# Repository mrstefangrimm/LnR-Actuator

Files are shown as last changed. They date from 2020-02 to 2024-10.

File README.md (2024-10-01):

# LnR-Actuator
The linear and rotary (LnR) actuator is a electromechanical device that allows linear as well as rotary motion of the shaft.

## Project History
A first revision was released in 2018. The construction has been simplified and made stiffer since then. All *[released revisions](https://github.com/mrstefangrimm/LnR-Actuator/releases)* are mechanical compatible. 

## Construction
A detailed description how to build a LnR-Actuator is published on *[Instructables.com](https://www.instructables.com/id/Linear-and-Rotation-Actuator/)* and [instructions for rev. 4 with brass bearings](https://www.instructables.com/Linear-and-Rotary-Actuator-With-Brass-Bearings/). 

## Manufacturing Tool Chain

| Software | License |
| --- | --- |
| SketchUp | SketchUp Shop |
| Ultimaker Cura | GPL |

## Software Tool Chain

| Application | License |
| --- | --- |
| lnr | Apache license |

| Tool | License |
| --- | --- |
| Visual Studio Code  | Microsoft license  |

| Library | Licence |
| --- | --- |
| angular | MIT license |
| Node.js | MIT license |

## Reference Projects

 - *[Marker Motion X-Ray Imaging Phantom](https://github.com/mrstefangrimm/GRIS5A)*
 - *[Liver Deformation X-Ray Imaging Phantom](https://github.com/mrstefangrimm/No2)*
 - *[Lung Motion X-Ray Imaging Phantom](https://github.com/mrstefangrimm/No3)*

## License


This work is licensed under the Creative Commons Attribution-ShareAlike 4.0 International License. To view a copy of this license, visit http://creativecommons.org/licenses/by-sa/4.0/ or send a letter to Creative Commons, PO Box 1866, Mountain View, CA 94042, USA.

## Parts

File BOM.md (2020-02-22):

Anz. | Beschreibung
---- | ------------ 
1 | Standard Servo Motor Tower Pro MG946R mit mitgeliefertem Servo Arm, 4 Befestigungsschrauben und vier Messinghülsen
1 | Micro Servo Motor Tower Pro MG90S mit mitgeliefertem Servo Arm und 2 Befestigungsschrauben
2 | Stahl Rundprofil d4 x 166 mit M4 x 15 Gewinde an einer Seite
1 | Stahl Rundprofil d4 x 14 mit Seegerringkerben mit Abstand 8 mm
1 | Stahl Rundprofil d4 x 12
1 | Holz Rundprofil d6 x 120
11 | M2 x 10 Universal Senkkopfschraube mit S-Spitze
4 | M4 Unterlagsscheibe
6 | M4 Mutter
2 | Seegerring d4
1 | Bueroklammer d1
1 | LnR-ChassisLinks oder LnR-ChassisRechts
1 | LnR-ChassisHaube
1 | LnR-ReiterLinks oder LnR-ReiterRechts
1 | LnR-ReiterLinksDeckel oder LnR-ReiterRechtsDeckel
1 | LnR-Flansch-Kreuz
1 | LnR-Verlaengerung
2 | LnR-SchraubVerstaerkung



This work is licensed under the Creative Commons Attribution-ShareAlike 4.0 International License. To view a copy of this license, visit http://creativecommons.org/licenses/by-sa/4.0/ or send a letter to Creative Commons, PO Box 1866, Mountain View, CA 94042, USA.

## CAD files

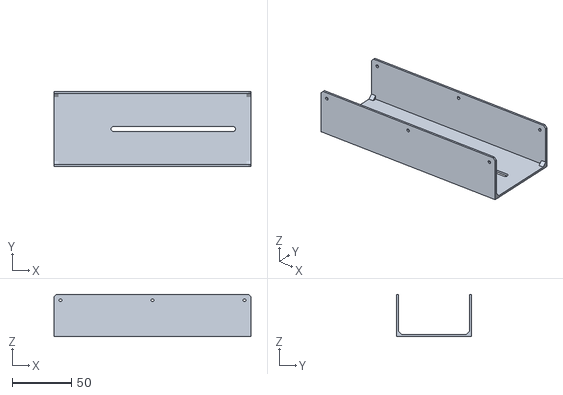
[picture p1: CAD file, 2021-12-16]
Instructable/Rev4/STLFiles/LnR-Cover.stl
166.0 x 63.2 x 35.6

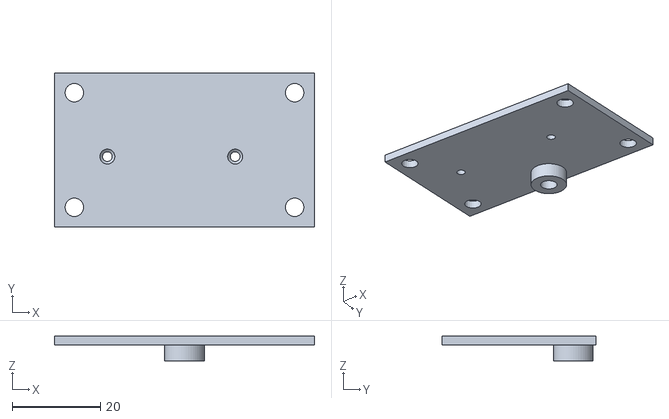
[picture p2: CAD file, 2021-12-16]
Instructable/Rev4/STLFiles/LnR-CarriageLeftLid.stl
59.0 x 35.0 x 5.60

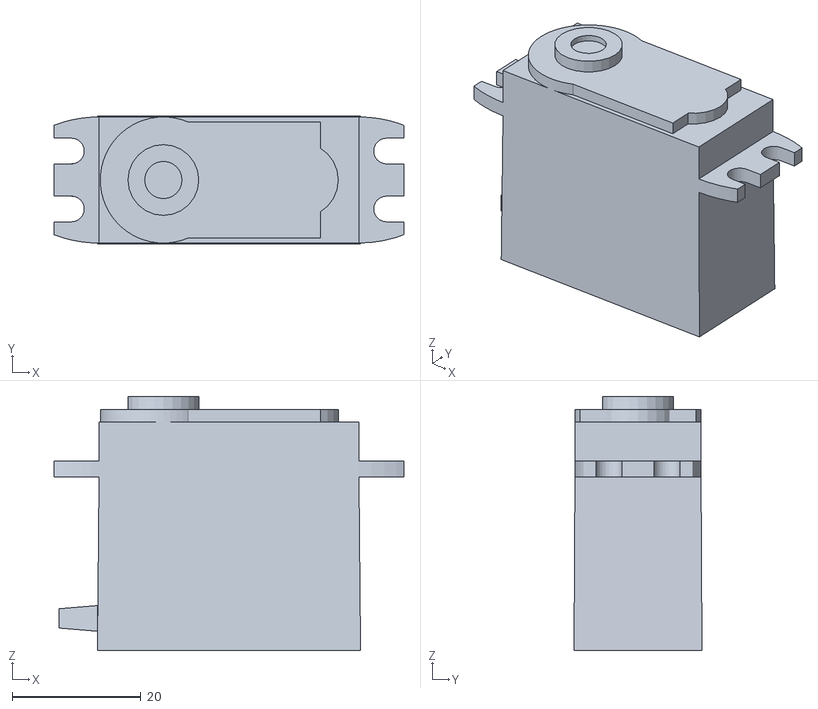
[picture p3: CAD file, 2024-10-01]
Soffware/lnr/public/LnR-VirmsGroupStaticBaseAnthracite.obj
54.4 x 19.9 x 39.5

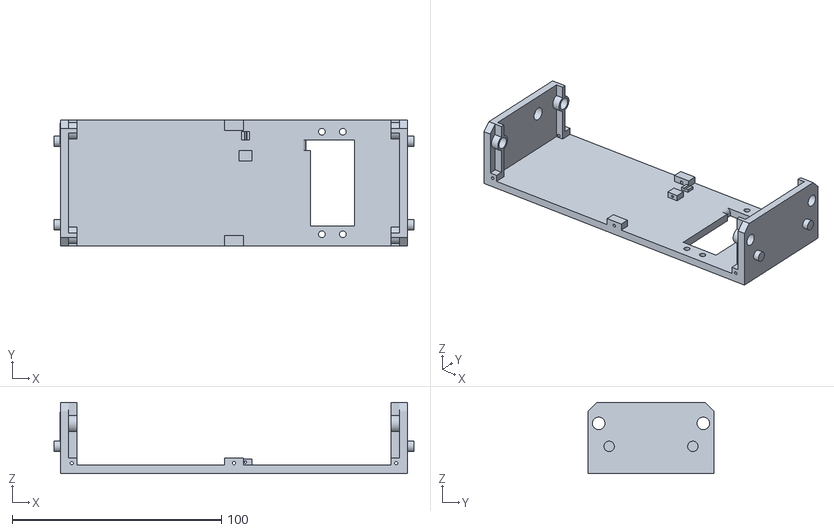
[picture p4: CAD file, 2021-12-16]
Instructable/Rev4/STLFiles/LnR-BaseLeft-Rev4.stl
172.0 x 60.0 x 34.0

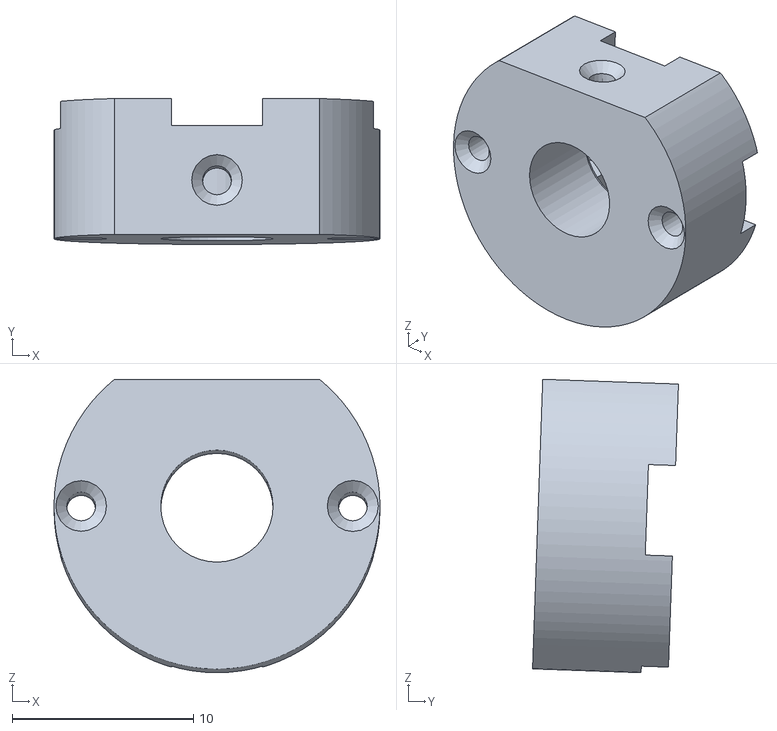
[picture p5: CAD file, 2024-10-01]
Soffware/lnr/public/LnR-VirmsGroupRotationBlue.obj
18.0 x 8.06 x 16.2

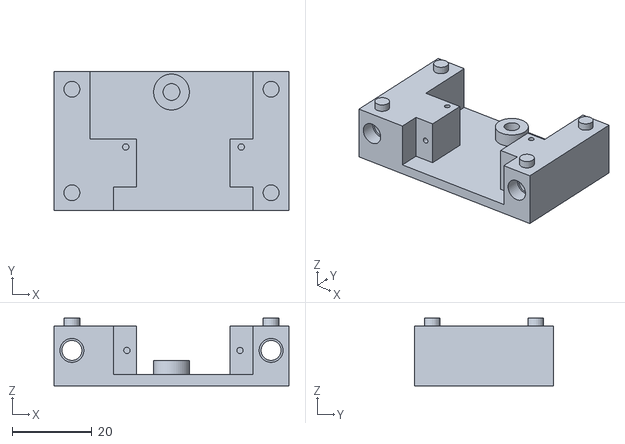
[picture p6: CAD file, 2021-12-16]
Instructable/Rev4/STLFiles/LnR-CarriageRight-JX9180MG.stl
59.0 x 35.0 x 17.0

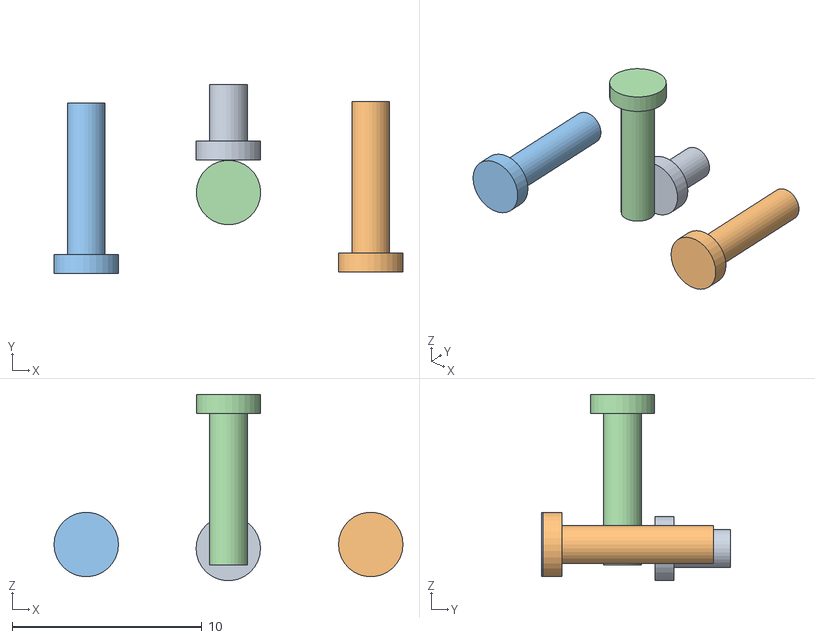
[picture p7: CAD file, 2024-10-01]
Soffware/lnr/public/LnR-VirmsGroupRotationSilver.obj
18.4 x 9.98 x 9.81
Lib_M2x3_1_1
Lib_M2x8_1_1
Lib_M2x8_1_2
Lib_M2x8_1_3

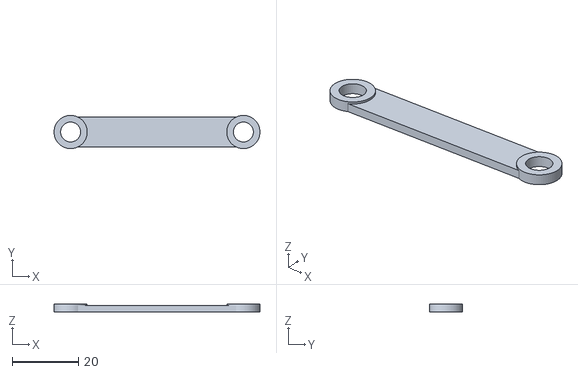
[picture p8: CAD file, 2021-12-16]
Instructable/Rev4/STLFiles/LnR-ExtensionArm-Rev4.stl
62.0 x 10.0 x 2.50

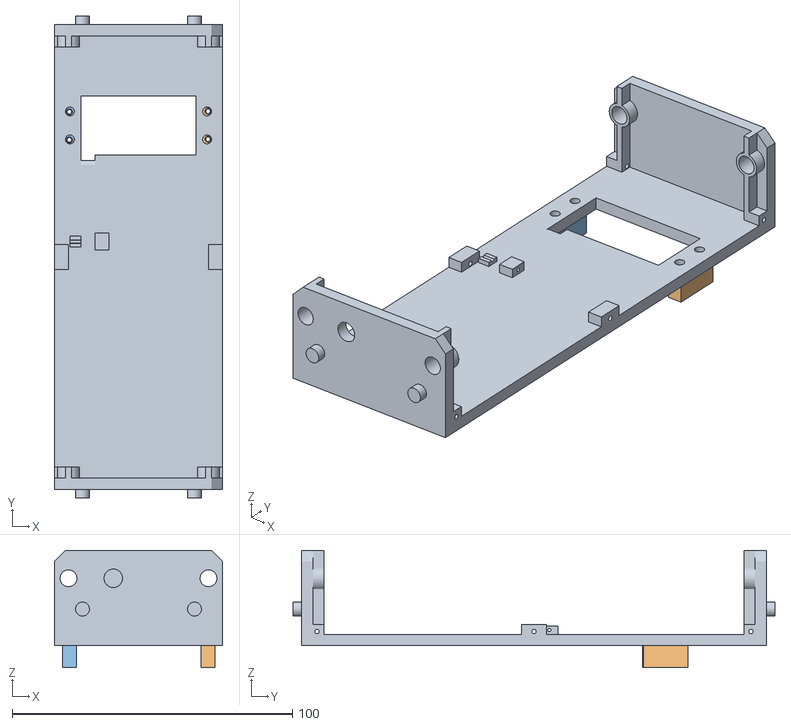
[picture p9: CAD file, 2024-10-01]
Soffware/lnr/public/LnR-VirmsGroupStaticBaseBlue.obj
60.0 x 172.0 x 42.0
LnR_ChassisLinks_Rev4_1
LnR_SchraubVerstaerkung1
LnR_SchraubVerstaerkung2

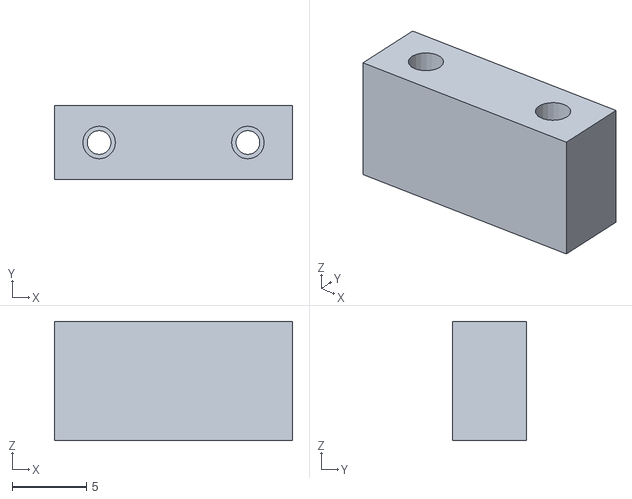
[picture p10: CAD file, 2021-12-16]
Instructable/Rev4/STLFiles/LnR-ServoFixationBlock.stl
16.0 x 5.00 x 8.00

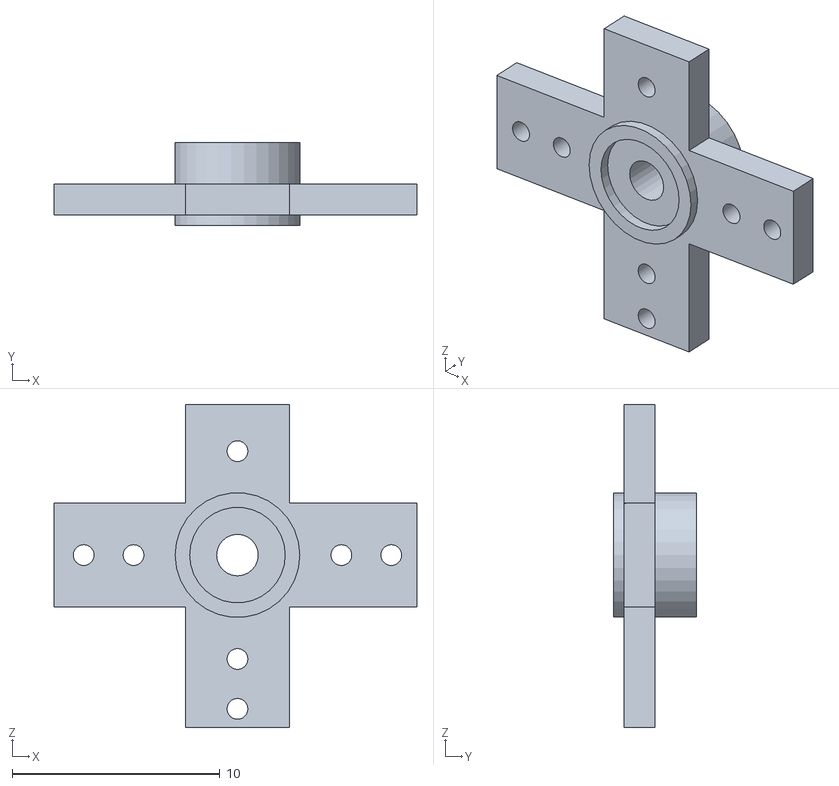
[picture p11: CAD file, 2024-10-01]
Soffware/lnr/public/LnR-VirmsGroupRotationWhite.obj
17.5 x 4.00 x 15.6

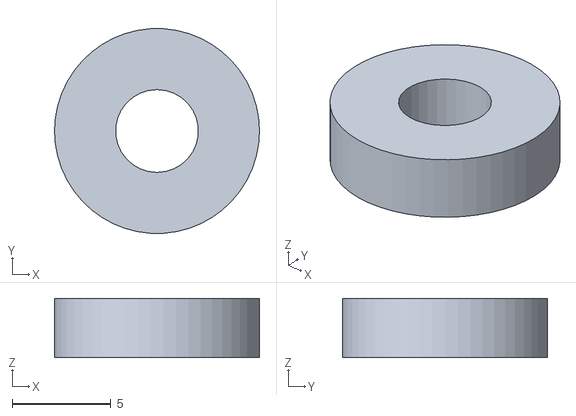
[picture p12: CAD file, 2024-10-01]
Soffware/lnr/public/LnR-VirmsGroupServoArmBlue.obj
10.4 x 10.4 x 3.00

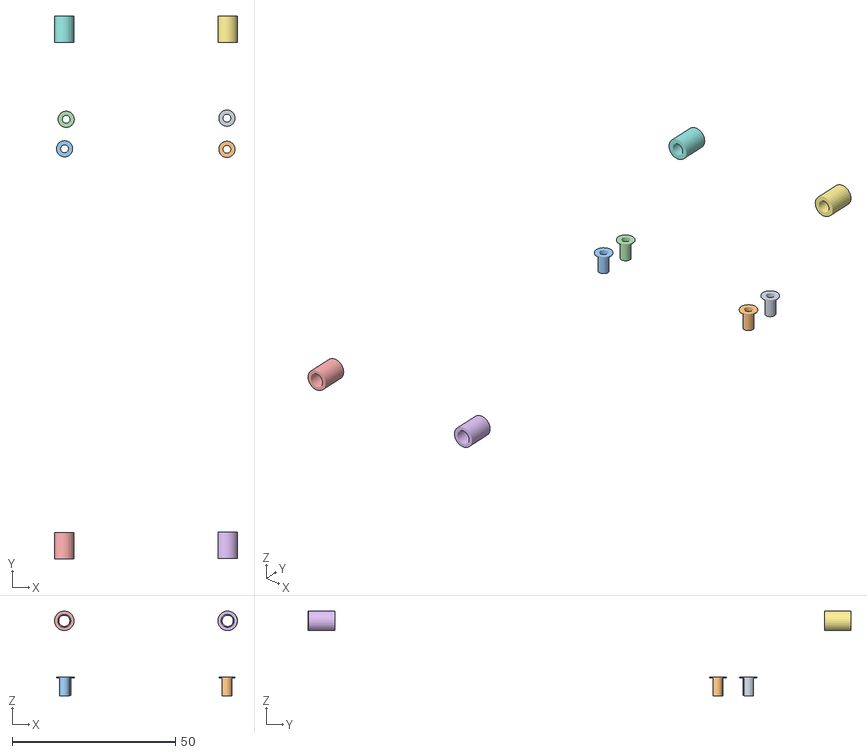
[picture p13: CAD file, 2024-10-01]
Soffware/lnr/public/LnR-VirmsGroupStaticBaseGold.obj
56.0 x 166.1 x 26.0
Lib_MG996R_BrassSleeve1
Lib_MG996R_BrassSleeve2
Lib_MG996R_BrassSleeve3
Lib_MG996R_BrassSleeve4
LnR_BrassSleeve_6x4x8_1
LnR_BrassSleeve_6x4x8_2
LnR_BrassThreadedSleeve_6x3_3x8_1
LnR_BrassThreadedSleeve_6x3_3x8_2

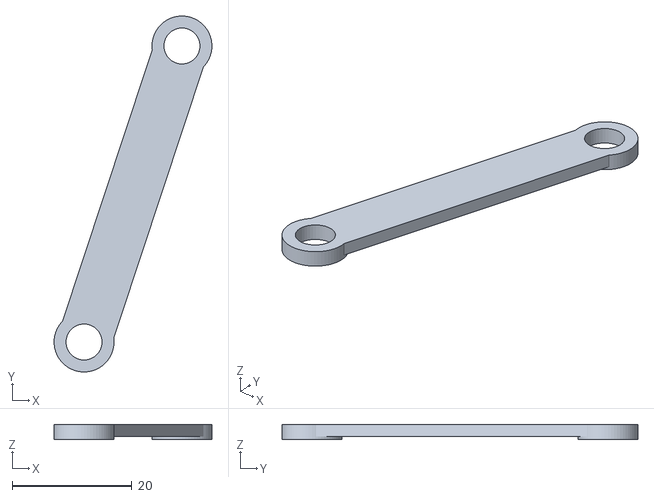
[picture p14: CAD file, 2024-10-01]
Soffware/lnr/public/LnR-VirmsGroupExtensionArm.obj
26.3 x 59.4 x 2.50

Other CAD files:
Soffware/lnr/public/LnR-VirmsGroupStaticCoverBlue.obj
Instructable/Rev4/STLFiles/LnR-CarriageLeft-JX9180MG.stl
Instructable/Rev4/STLFiles/LnR-BaseRight-Rev4.stl
Instructable/Rev4/STLFiles/LnR-ServoArmFixationRing.stl
Accessories/Sketchup/Cmn-FlanschHalter.skp
Accessories/Sketchup/Gris5a-Flansch.skp
Accessories/Sketchup/LnR-Calibration-Basis.skp
Accessories/Sketchup/LnR-Calibration-Messaufsatz.skp
Instructable/Rev3/STLFiles/LnR-BaseLeft.stl
Instructable/Rev3/STLFiles/LnR-BaseRight.stl
Instructable/Rev3/STLFiles/LnR-CarriageLeft.stl
Instructable/Rev3/STLFiles/LnR-CarriageLeftLid.stl
Instructable/Rev3/STLFiles/LnR-CarriageRight.stl
Instructable/Rev3/STLFiles/LnR-CarriageRightLid.stl
Instructable/Rev3/STLFiles/LnR-Cover.stl
Instructable/Rev3/STLFiles/LnR-ExtensionArm.stl
Instructable/Rev3/STLFiles/LnR-Flange.stl
Instructable/Rev3/STLFiles/LnR-ServoArmFixationRing.stl
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

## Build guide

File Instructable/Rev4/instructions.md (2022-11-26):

# Linear and Rotary Actuator With Brass Bearings

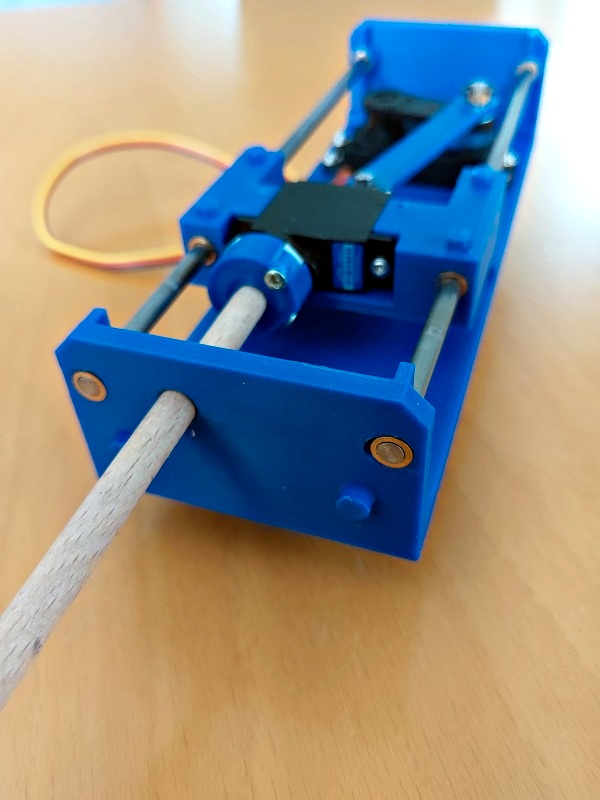
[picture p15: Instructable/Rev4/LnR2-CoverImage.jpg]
LnR2-CoverImage


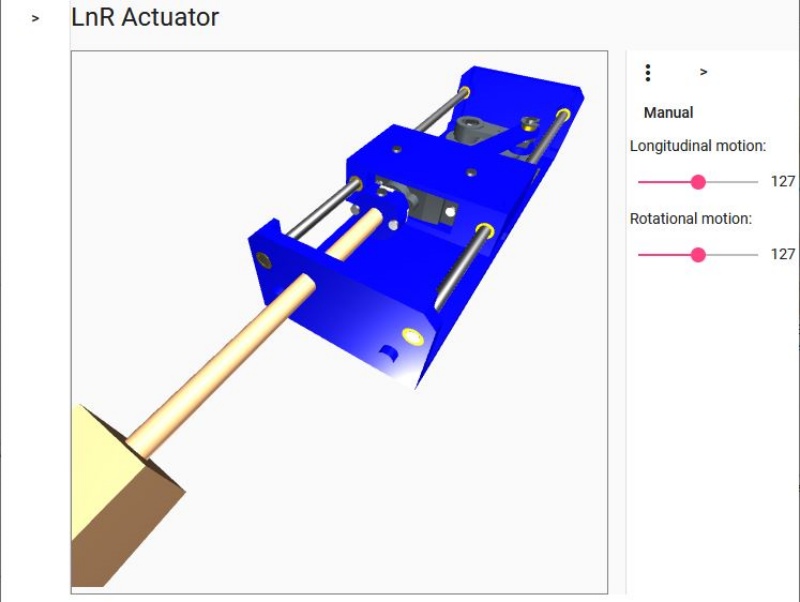
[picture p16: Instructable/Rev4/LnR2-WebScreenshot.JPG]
LnR2-WebScreenshot


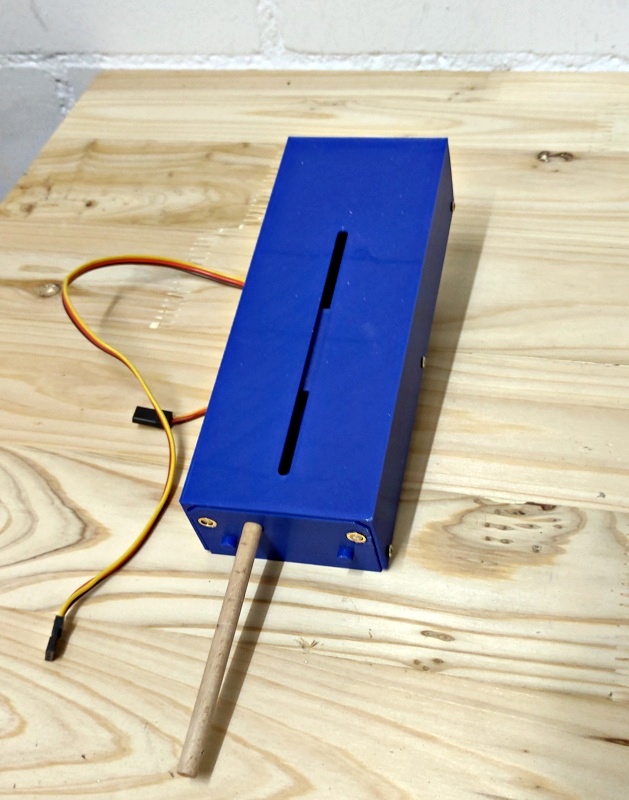
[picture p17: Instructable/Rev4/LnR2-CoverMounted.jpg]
LnR2-CoverMounted


The Linear and Rotary (LnR) actuator is a linear servo with a rotatable shaft. This means you can move an  object forwards and backwards and rotate it at the same time. It is  possible to move an object 45 mm back and forth and rotate it 180 degrees.

To get an idea, check out the [3D model of the LnR Actuator](https://mrstefangrimm.github.io/). With the two sliders on the right you can simulate longitudinal and rotational motion.

The used motors are two commercially available servo motors. Beside the low price, servos have a useful characteristic: Servos have already integrated control logic in order to be absolutely positioned. Additional position read-out modules are therefore not required.

To  build it you need a lathe and metal drills (4.1 and 3.3 mm) to manufacture the sleeve bearings. A turning tool to create the snap ring notch is also required. Further you need a M4 screw tap and a M4 thread cutter.

This is a improved version of the [Linear and Rotary Actuator](https://www.instructables.com/Linear-and-Rotation-Actuator/). The advantages are:

- It makes less noise
- It is more accurate because it has less mechanical play and less friction

To build this improved version of the LnR Actuator, you will need a lathe to manufacture the sleeve bearings. The original LnR Actuator was explicitly designed so that it can be manufactured with of-the-shelve components.

The direct material costs are approximately USD 30.

**Supplies**

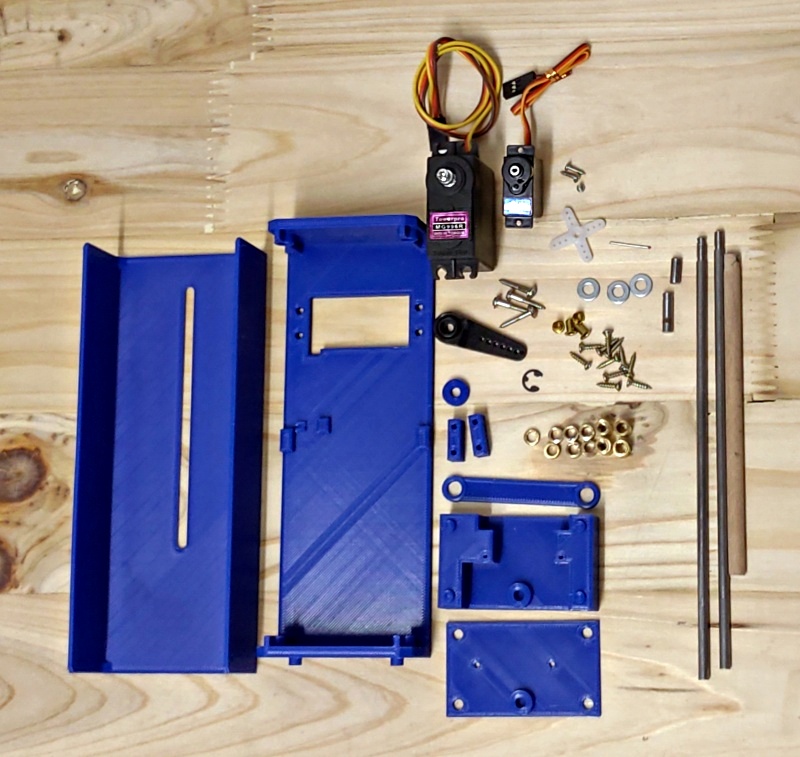
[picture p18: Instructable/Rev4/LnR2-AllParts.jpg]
LnR2-AllParts


 1 Standard Servo Tower Pro MG946R. Comes with servo arm, 4 M2 mounting screws and 4 d3 brass sleeves

 1 Micro Servo JX PDI 9180MG. Comes  with servo arm and 2 mounting screws 

11 M2 x l10 mm flat headed screw

 2 Brass sleeve d6 x l8

 2 Threaded brass sleeve d6 x l8

 4 Brass sleeve d6 x l4

 2 Brass sleeve d6 x l3

 1 Brass sleeve d6 x l2

 3 M4 washer

 1 Snap ring d4

 1 Paperclip d1

 1 Wooden rod 6 x l120 

 2 Steel shaft d4 x l166 with M4 x l8 thread on one end 

 1 Steel rod d4 x l15 with a snap ring notch 

 1 Steel rod d4 x l12

 1 3D Printer

 105g PLA filament

 1 Lathe machine

 Legend: l:length in millimeters, d:diameter in millimeters

## Step 1: 3D Printed Parts

You either need to print the left-sided or  right-sided parts. The pictures in this Instructable show a left-sided  LnR Actuator.

You can use PLA with 20% infill. If you do not have a 3D printer, I recommend looking for a 3D printing service nearby.

## Step 2: Rotary Drive

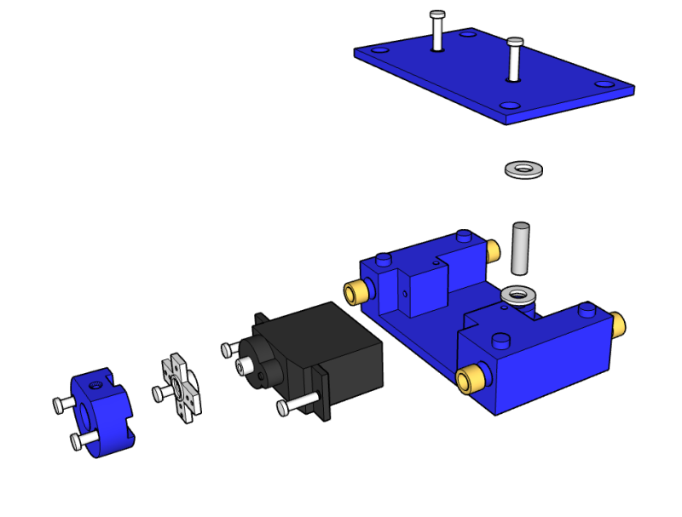
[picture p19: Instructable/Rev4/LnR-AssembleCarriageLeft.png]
LnR-AssembleCarriageLeft


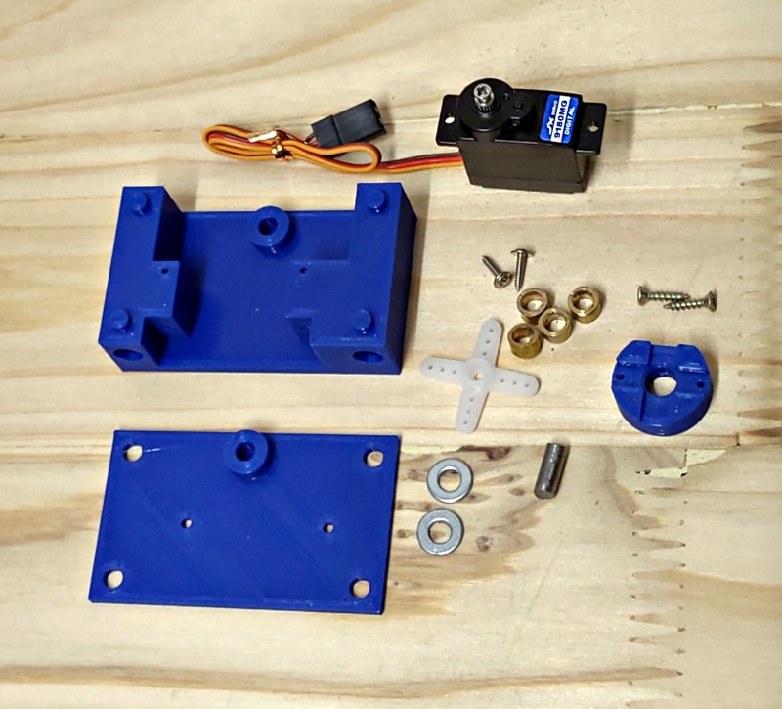
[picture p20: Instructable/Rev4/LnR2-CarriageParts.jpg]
LnR2-CarriageParts


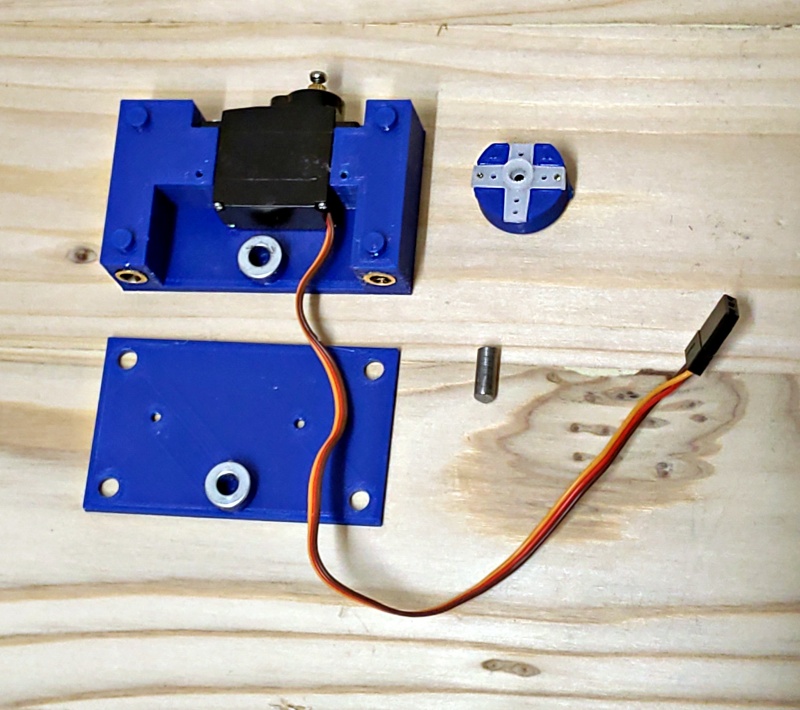
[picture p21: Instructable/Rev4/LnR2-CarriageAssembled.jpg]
LnR2-CarriageAssembled


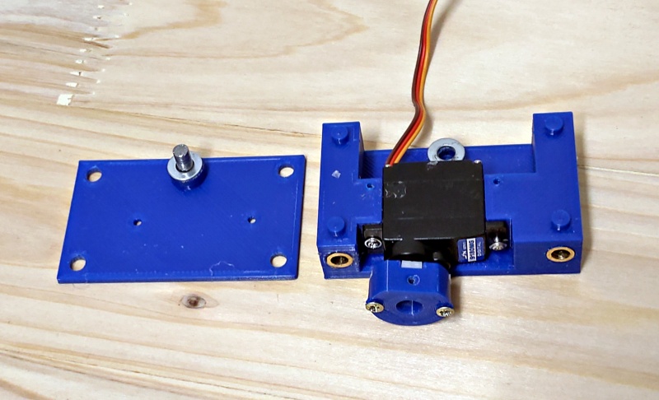
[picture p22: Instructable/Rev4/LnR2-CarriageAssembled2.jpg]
LnR2-CarriageAssembled2


Press the 4 mm long brass sleeves into the printed carriage component. This is best done in a vice. Mount the micro servo with the supplied screws.

Use 2 M2 screws to attach the supplied servo cross arm to the printed flange.

Glue 2 M4 washers onto the carriage and the carriage lid.

## Step 3: Linear Drive

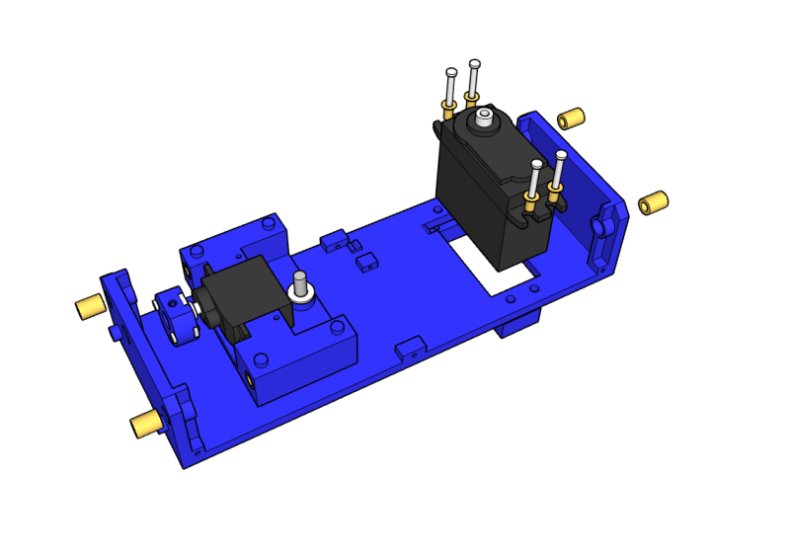
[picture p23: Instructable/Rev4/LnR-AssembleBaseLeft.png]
LnR-AssembleBaseLeft


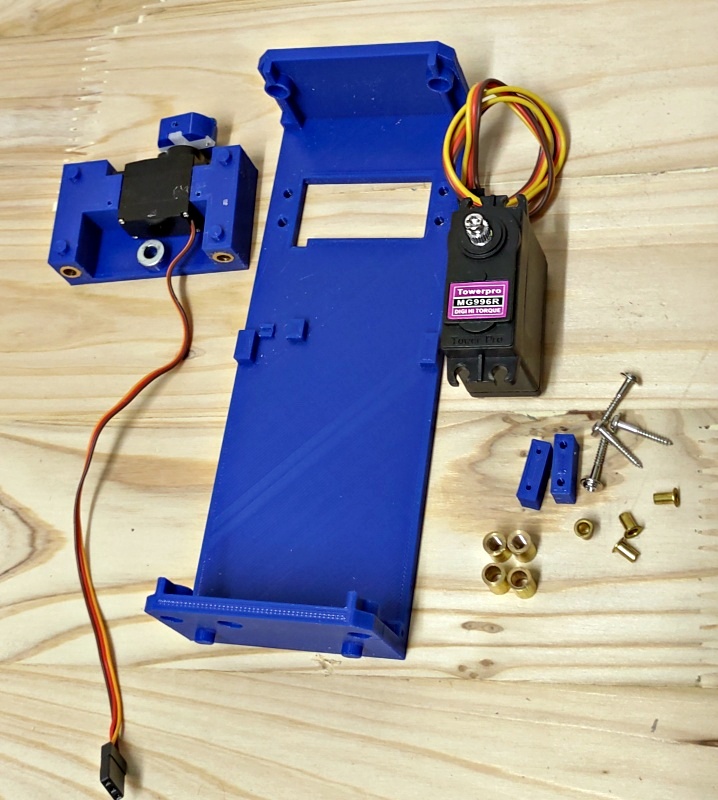
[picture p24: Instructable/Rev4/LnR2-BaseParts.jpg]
LnR2-BaseParts


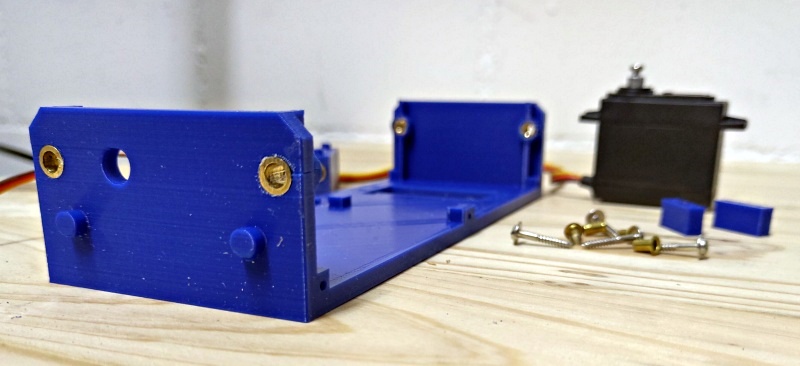
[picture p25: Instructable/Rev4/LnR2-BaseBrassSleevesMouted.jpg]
LnR2-BaseBrassSleevesMouted


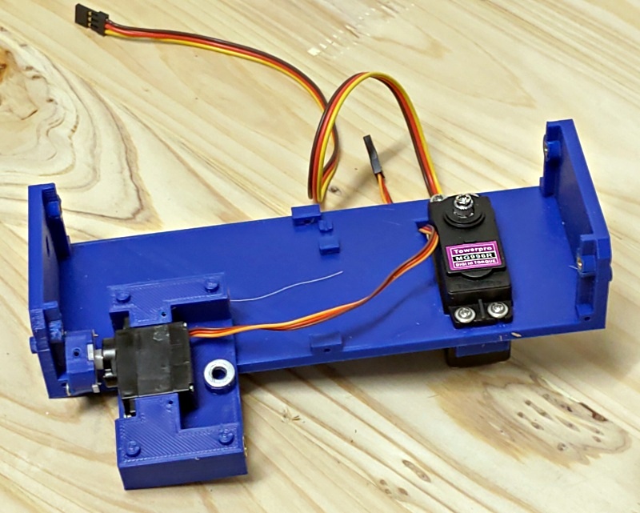
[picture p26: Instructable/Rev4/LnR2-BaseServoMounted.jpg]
LnR2-BaseServoMounted


Press the 8 mm long brass sleeves into the printed base component. This is best done in a vice. The plain sleeves are mounted to the front and the threaded sleeves are mounted to the rear plane.

Attach the standard servo motor the the printed base component. In order to bring the servo through the opening, you need to  remove its bottom cap and bend the cable down. As shown in the picture, the cable of the micro servo has to go through the intended opening first. For fastening the servo motor, use supplied screws and brass hulls and the two printed servo fixation blocks.

## Step 4: Longitudinal Guides

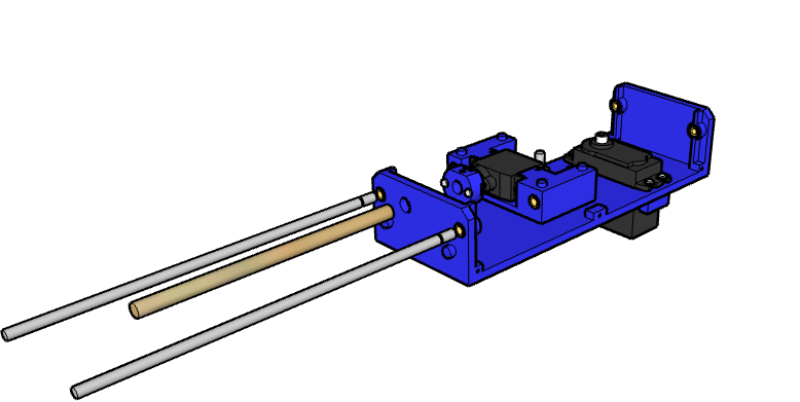
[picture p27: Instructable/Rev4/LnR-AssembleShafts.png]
LnR-AssembleShafts


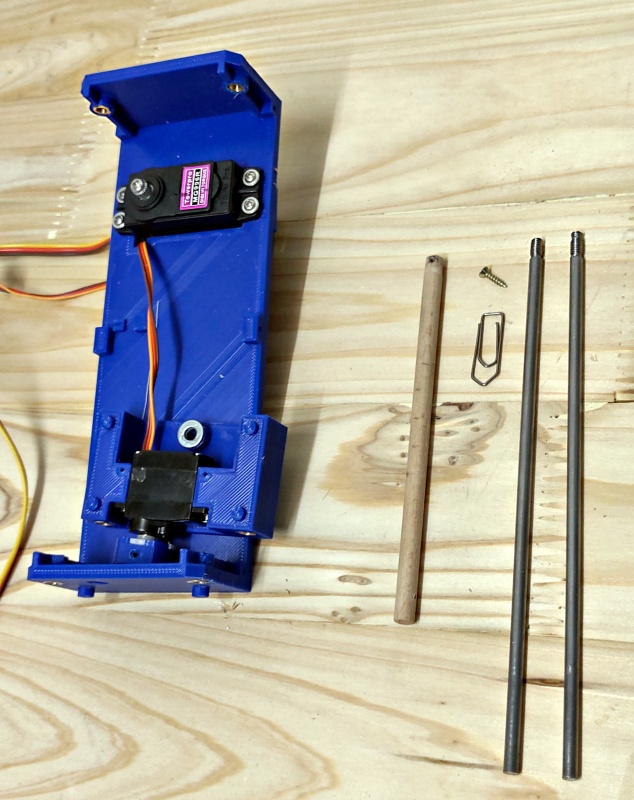
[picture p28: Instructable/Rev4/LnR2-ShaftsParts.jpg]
LnR2-ShaftsParts


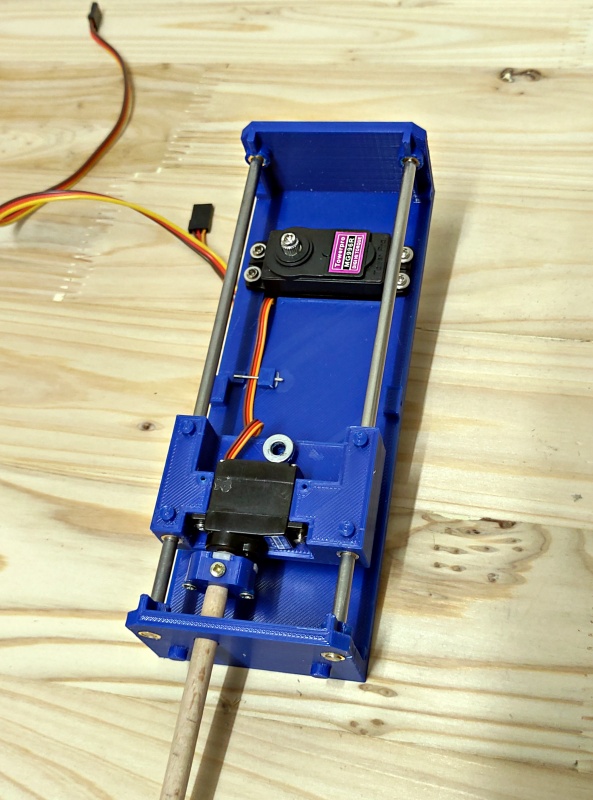
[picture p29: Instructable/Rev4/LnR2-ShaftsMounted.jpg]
LnR2-ShaftsMounted


Slide the metal shafts from the front through the sleeve bearings of the base component and the carriage component. Then screw the shafts into the threaded sleeves on rear plane of the base component.

Attach the wooden rod the flange with a M2 screw. Drill a 1.5 mm hole into the wooden rod where the screw goes through, otherwise the wood will break.

Use one leg of the paperclip to fixate the cable of the micro servo the the base component.

## Step 5: Force Transmission

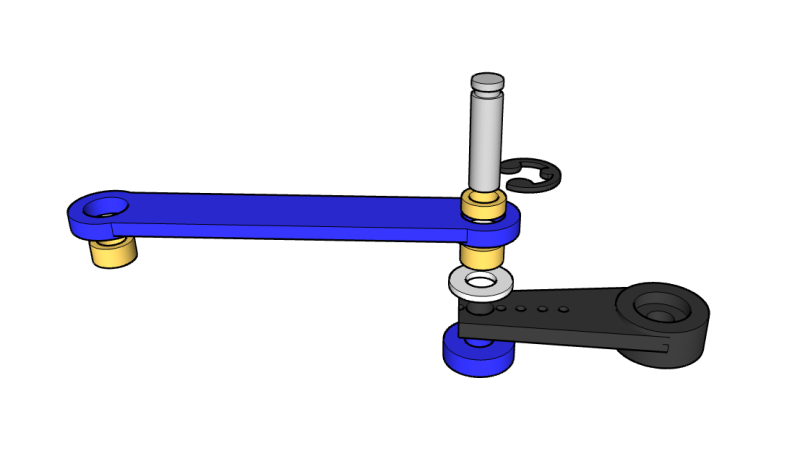
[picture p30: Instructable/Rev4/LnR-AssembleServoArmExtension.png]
LnR-AssembleServoArmExtension


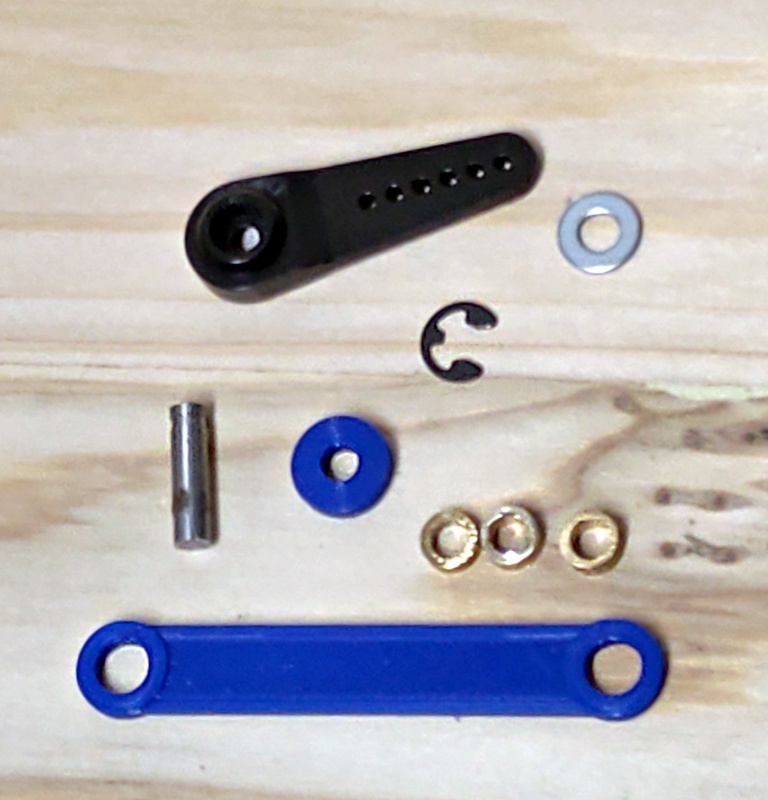
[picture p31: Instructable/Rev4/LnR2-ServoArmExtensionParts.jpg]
LnR2-ServoArmExtensionParts


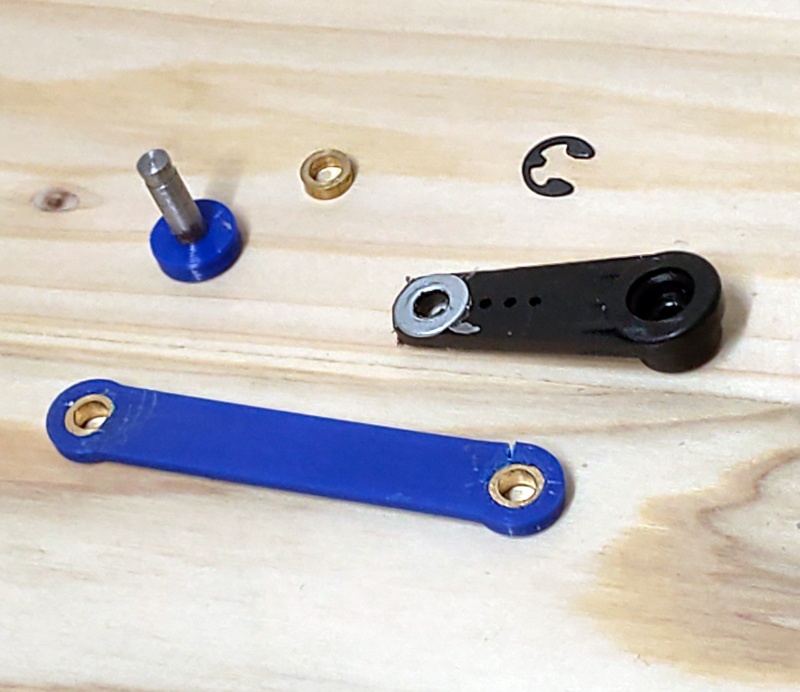
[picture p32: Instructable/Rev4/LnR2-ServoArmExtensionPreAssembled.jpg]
LnR2-ServoArmExtensionPreAssembled


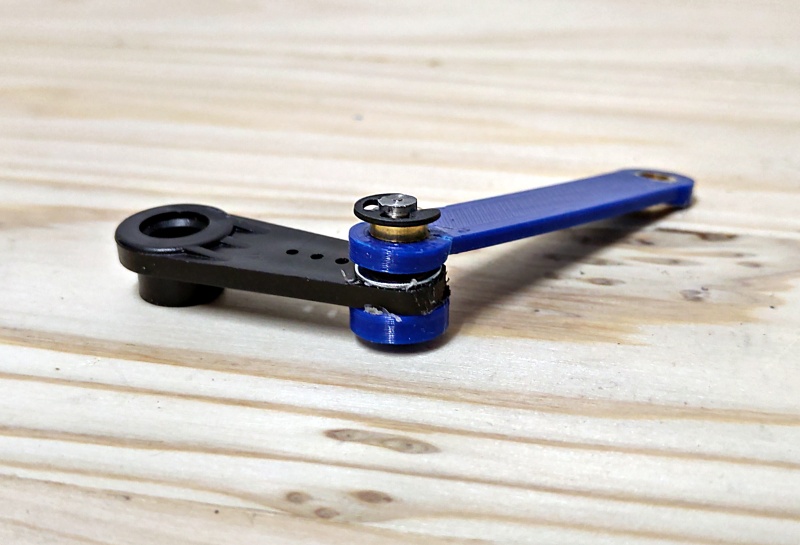
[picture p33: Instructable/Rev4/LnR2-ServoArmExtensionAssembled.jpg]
LnR2-ServoArmExtensionAssembled


Press the 3 mm long brass sleeves into the printed servo arm extension component. Press metal rod with the snap ring notch into the printed fixation ring.

Drill a 4.1 mm hole into the supplied servo arm and glue a M4 washers onto the servo arm.

Put all the components together and add the snap ring for fixation.

## Step 6: Finalization

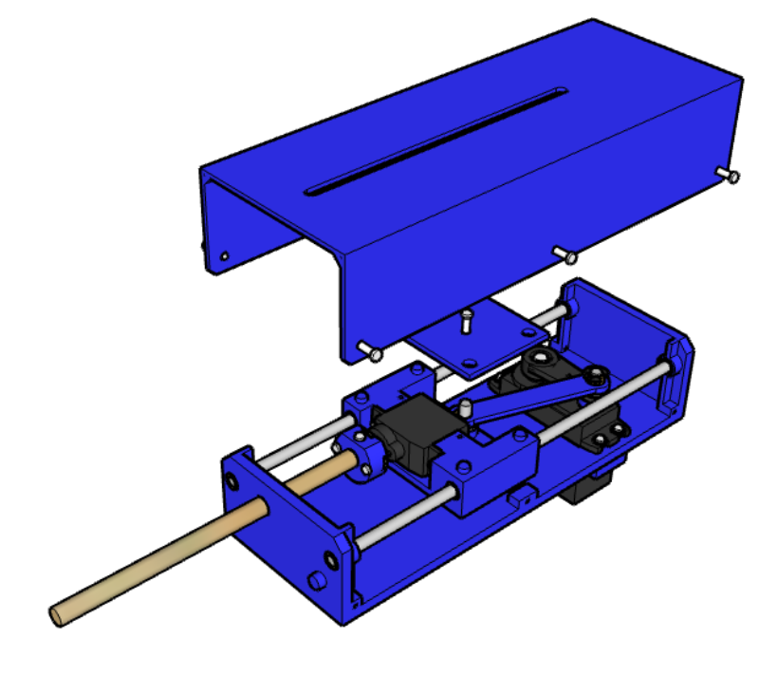
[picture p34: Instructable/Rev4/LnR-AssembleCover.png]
LnR-AssembleCover


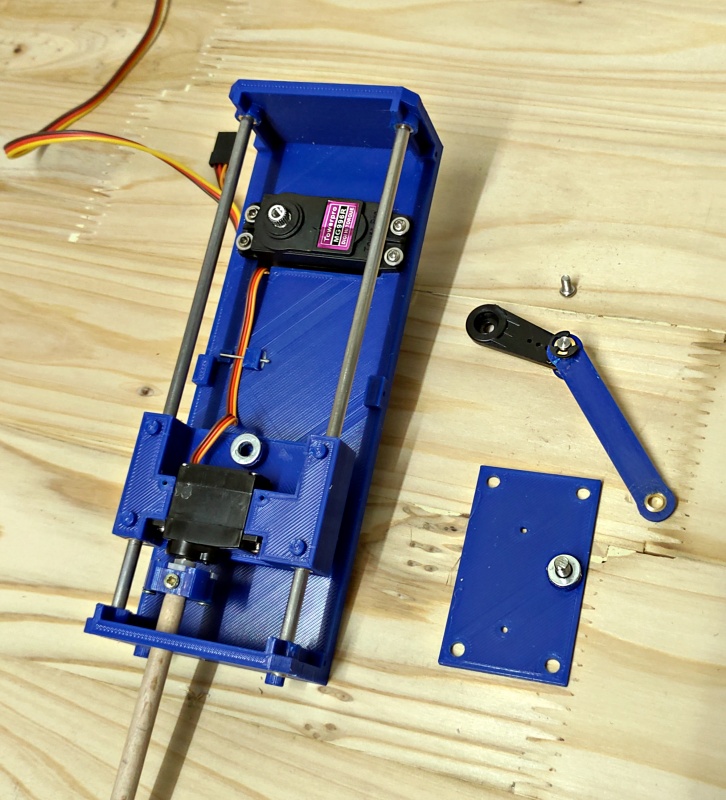
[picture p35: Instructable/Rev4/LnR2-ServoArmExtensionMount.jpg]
LnR2-ServoArmExtensionMount


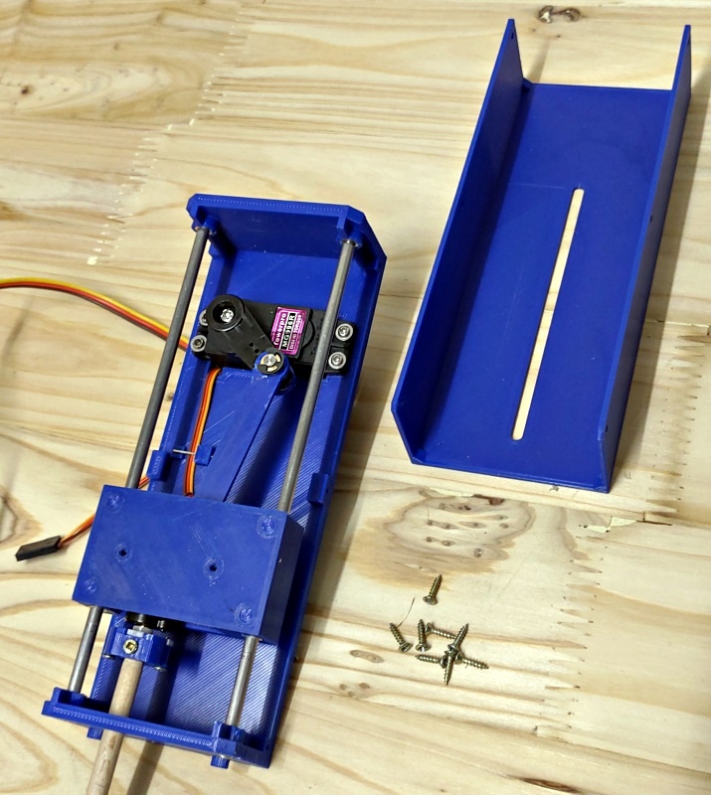
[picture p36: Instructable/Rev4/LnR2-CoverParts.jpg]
LnR2-CoverParts


LnR2-CoverMounted

Position the servo motor to middle position and mount the servo arm to the servo motor. Move the carriage to the position where bore of the extension arm matches with the bore of the carriage. Attach the extension arm with the 12 mm long metal rod and mount the carriage's lid with two M2 screws.

Mount the cover to the base component with six M2 screws.

That is the LnR Actuator!

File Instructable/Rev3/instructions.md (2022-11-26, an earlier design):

# Linear and Rotary Actuator

https://www.youtube.com/embed/AOaQP5htdsE?feature=oembed&autoplay=1

This Instructable is about how to make a  linear actuator with a rotatable shaft. This means you can move an  object forwards and backwards and rotate it at the same time. It is  possible to move an object 45 mm back and forth and rotate it 180 degrees.

The used motors are two commercially available servo motors. Beside the low price servos have a useful characteristic: Servos have already integrated control logic to be absolutely positioned. Additional position read-out modules are therefore not required. For the Arduino [1], there is its Servo library [2]. I am sure other platforms have similar libraries.

To  build it you need a standing drill machine and a 4.2 mm metal drill. You are going to drill out M4 nuts. These are going to be your sleeve bearings.

To cut the threads on the metal shafts, you need a good bench vice and a M4 thread cutter. And also a M4 screw tap for the fixation of the shafts is required.

The costs are approximately USD 35. All the parts can be either 3D printed or bought in a hardware store.

**Supplies**

 1 Standard Servo Tower Pro MG946R. Comes with servo arm, 4 M2 mounting screws and 4 d3 brass sleeves

 1 Micro Servo Tower Pro MG90S. Comes  with servo arm and 2 mounting screws 

11 M2 x l10 mm flat headed screw 

 4 M4 washer

 6 M4 nut

 1 Snap ring d4 mm

 1 Paperclip d1 mm 

 1 Wooden rod d6 x l120 

 2 Steel or aluminum shaft d4 x l166 with M4 x l8 thread on one end 

 1 Steel or aluminum rod d4 x l14 with a snap ring notch 

 1 Steel or aluminum rod d4 x l12 

 1 3D Printer

105g PLA filament

Legend: l:length in millimeters, d:diameter in millimeters

## Step 1: 3D Printed Parts

You either need to print the left-sided or  right-sided parts. The pictures in this Instructable show a left-sided  LnR Actuator (Looking from the front, the wooden rod is on the left  side).

You can use PLA with 20% infill. If you do not have a 3D printer, I recommend looking for a 3D printing service nearby.

## Step 2: Carriage Bearings

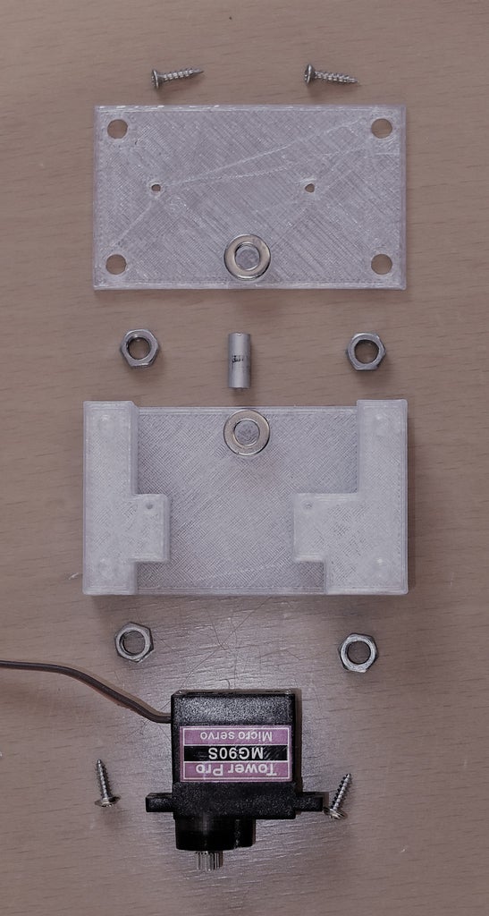
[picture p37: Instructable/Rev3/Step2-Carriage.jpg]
Step2-Carriage


As bearings, the M4 nuts are used! For that,  you drill out the (M4/3.3 mm) holes with the 4.2 mm metal drill. Press  the drilled out M4 nuts into the openings in the carriage.

Glue 2 M4 washers onto the carriage and the carriage lid.

## Step 3: Mirco Servo and Extension Arm

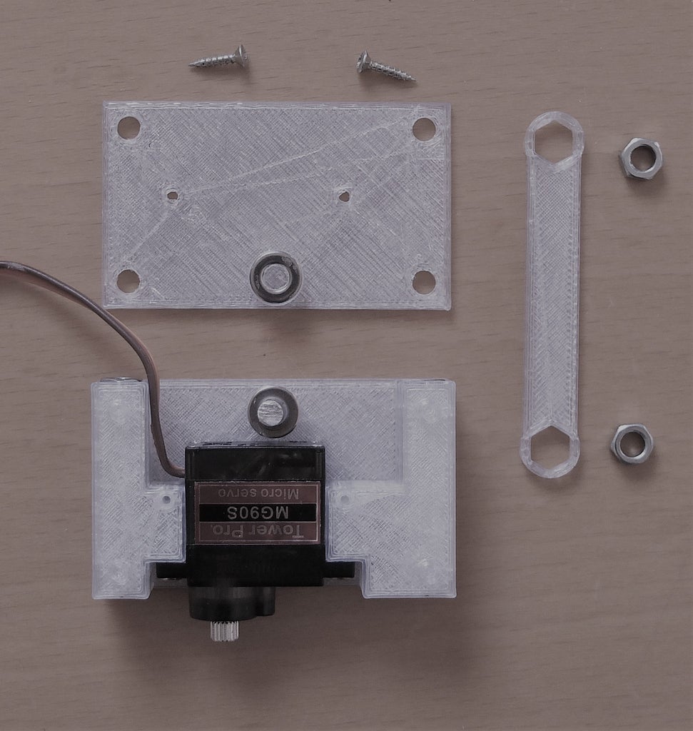
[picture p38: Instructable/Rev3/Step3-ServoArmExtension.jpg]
Step3-ServoArmExtension


Mount the Micro Servo onto the carriage.

On the right side you see the extension arm and the remaining 2 M4 nuts.  Press the drilled out M4 nuts into the openings of the extension arm.

## Step 4: Carriage and Rotatable Shaft

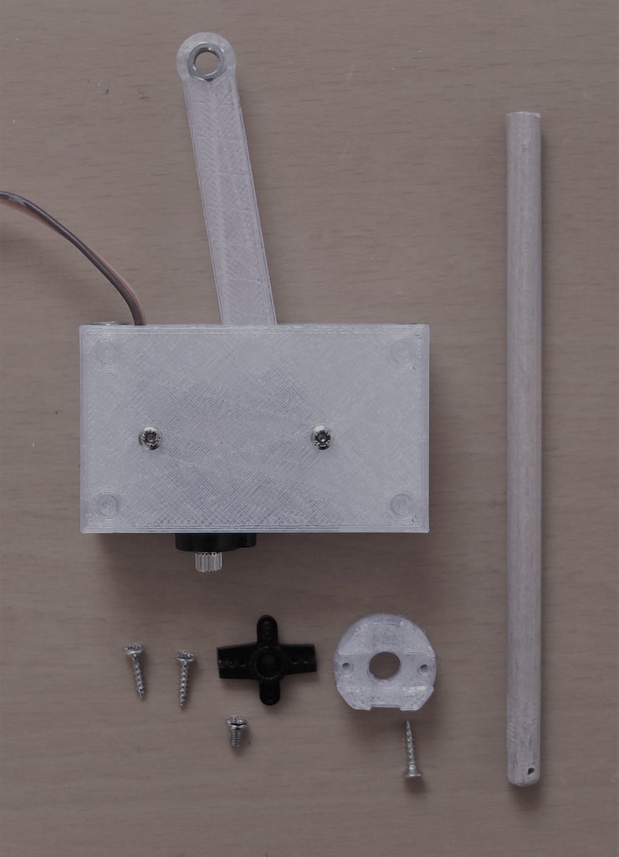
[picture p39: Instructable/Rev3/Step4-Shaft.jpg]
Step4-Shaft


Assemble carriage, extension arm and carriage lid. Use the small 12 mm long metal rod as the axis.

At the bottom of the picture you see the flange that is attached to the Micro Servo arm.

You need to drill a 1.5 mm hole into the wooden rod (bottom right of the picture), otherwise the wood will break.

## Step 5: Servo Joint

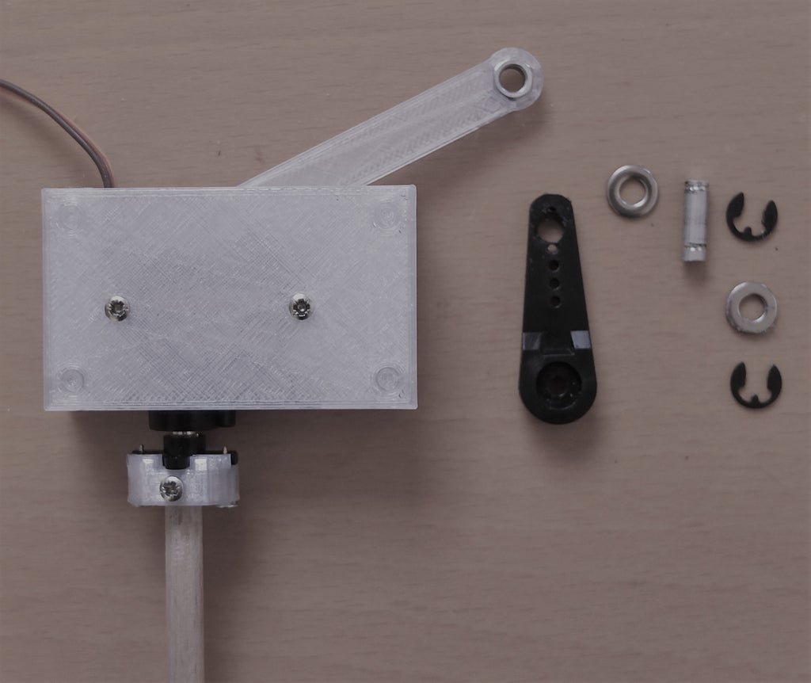
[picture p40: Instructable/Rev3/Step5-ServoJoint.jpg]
Step5-ServoJoint


Drill a 4.2 mm hole into the standard servo arm and add a notch to the 14 mm metal rod for the snap ring.

Glue one of the washers onto the servo arm.

This is how you stack the components from top to bottom:

1) Mount the snap ring onto the axis

2) Add a washer

3) Hold the servo arm under the extension arm and press the assembled axis through it.

4) Add some glue to the fixation ring and press it from the bottom onto the axis.

The picture is not up-to-date. Instead of the second snap ring it shout  show the fixation ring. The idea with the fixation ring is an  enhancement to the original design.

## Step 6: Servo Mount

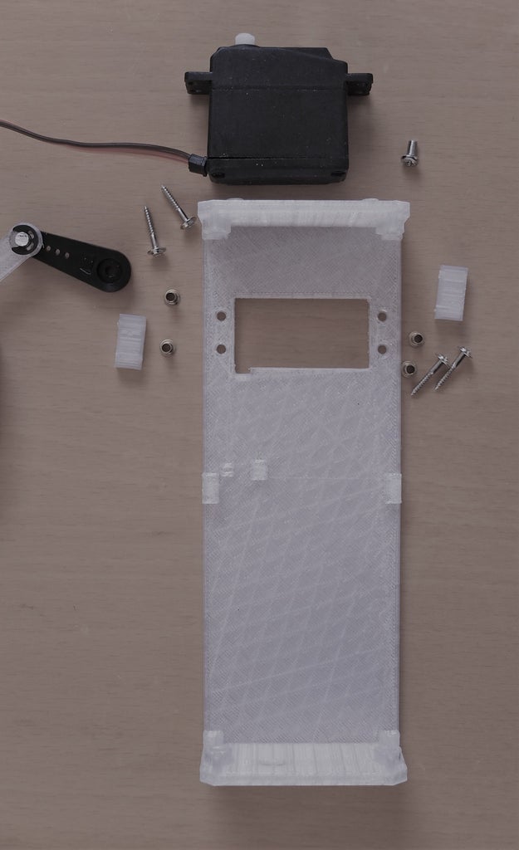
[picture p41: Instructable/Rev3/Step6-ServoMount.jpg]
Step6-ServoMount


The standard servo is attached to the  actuator. In order to bring the servo through the opening, you need to  remove its bottom cap so you can bend the cable down.

The mounting screws go into the messing sleeves first, then through the holes in the  actuator. Drill the screws into the fixation blocks which are put below  the LnR-Base.

## Step 7: Longitudinal Motion

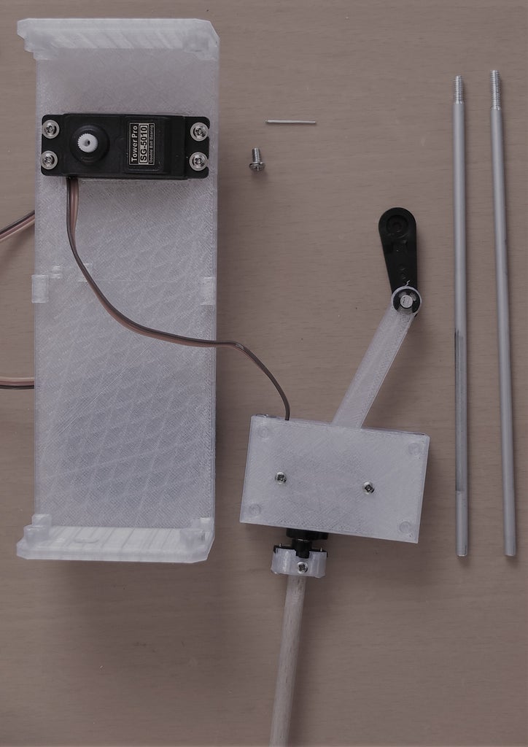
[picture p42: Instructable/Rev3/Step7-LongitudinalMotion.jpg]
Step7-LongitudinalMotion


With the M4 screw tap you cut a thread into the 3.3 mm holes of the back plane of the LnR-Base.

The carriage moves on the two metal rods. These rods are pushed through the 4.2 mm  front  holes of the LnR-Base, then through the carriage's bearings and  fixated with the M4 thread in the rear plane of the actuator.

## Step 8: Cover

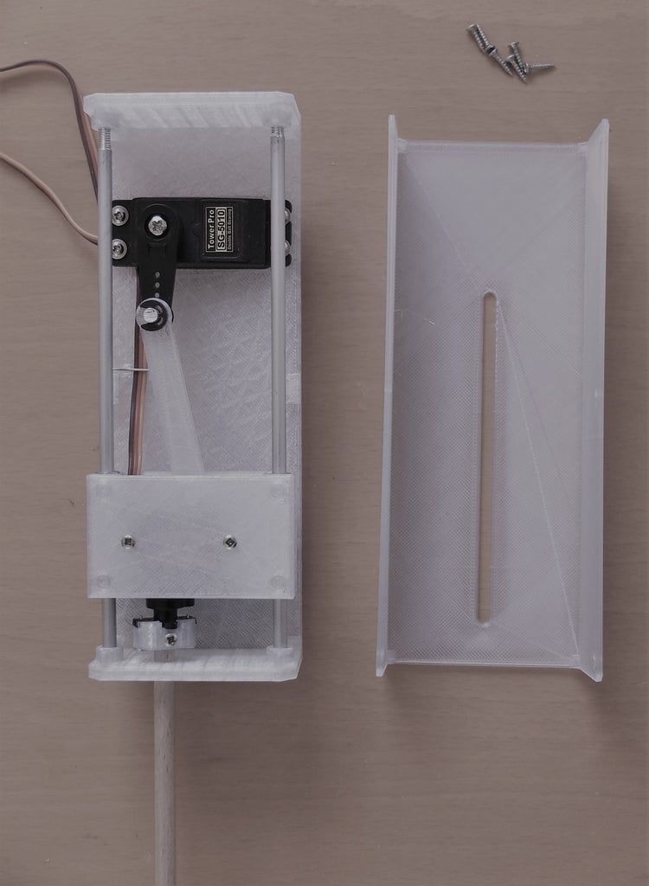
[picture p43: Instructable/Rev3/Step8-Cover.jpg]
Step8-Cover


That is the LnR Actuator!

To fix the Micro Servo cable, a part of a paper clip is used. Mount the hood onto the actuator and you are done.

## Step 9: Arduino Sketch (optional)

https://www.youtube.com/embed/eBcqPfLJKAA?feature=oembed&autoplay=1

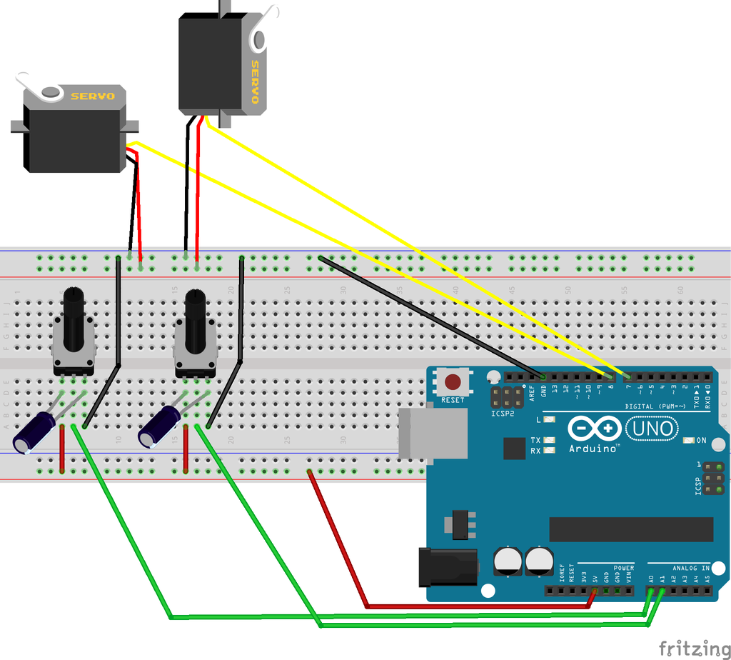
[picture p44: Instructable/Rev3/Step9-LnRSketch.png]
Step9-LnRSketch


Connect two potentiometers to the Arduino inputs A0 and A1. The signal pins are 7 for rotary and 8 for longitudinal motion.

It is important that you take the 5 Volts from the Arduino for the  potentiometers and not from the external 5 V power supply. To drive the  servos you have to use an external power supply.

## Step 10: Beyond a Programming Example (optional)

https://www.youtube.com/embed/KJdUGMOCTKk?feature=oembed&autoplay=1

This is how I cancel systematic errors in the  software that controls the LnR Actuator. By eliminating the positioning  error due to mechanical transformation and due to mechanical play, a  positioning accuracy of 0.5 millimeters in longitudinal direction and 1 degree in rotary motion is possible.

Mechanical transformation: Arduinos map function [5] can be written as: *f(x) = a + bx*. For the demo data set [6], the maximum deviation is 1.9 mm. This means  at some point, the position of the actuator is almost 2 millimeters away from the measured value. 

With a polynomial with a degree of 3, *f(x) = a + bx + cx^2 + dx^3*, the maximum deviation for the demo data is 0.3 millimeters; 6 times  more accurate. To determine the parameters a, b, c and d, you have to  measure at least 5 points. The demo data set has more than 5 measurement points, but 5 are sufficient. 

Mechanical play:  Due to  the mechanical play, there is an offset (called backlash) in the position if you move the  actuator first forwards and then backwards, or if you move it clockwise  and then counter clockwise. In the longitudinal direction, the actuator  has mechanical play in the two joints between the servo arm and the  carriage. For the rotary motion, the actuator has mechanical play between  the carriage and the shafts. The servo motors have also some mechanical  play themselves. 
To cancel the mechanical play, the rules are: 
  A) When moving forwards or clockwise, the formula is: *f(x) = P(x)*
  B) When moving backwards or counter clockwise, the formula is: *f(x) = P(x) + O(x)*

*P(x)* and *O(x)* are polynomials. B is the backlash that is added due to the mechanical  play. To determine the polynomial parameters, measure 5 points when  moving in one direction and the same 5 points when moving in the  opposite direction.

If you are planning to control multiple servo  motors with an Arduino and I convinced you to do a software calibration  using polynomials, have a look at my prfServo Arduino library [4].

For the pencil lead drive video the prfServo library was used. For each of  the four servos a five point calibration was done in both directions.

Other systematic errors: The actuator has additional systematic errors: Friction, eccentricity  and the resolution of the used servo library and servo motors.

Maybe, more as a fun fact, the resolution of the Adafruit Servo Shield [3] is  0.15 mm in longitudinal direction! Here is why: The servo shield uses  the PCA9685 chip to produce the PWM signal. The PCA9685 is designed to  create PWM signals between 0 and 100 % and has 4096 values for that. But for a servo, only values of lets says 200 (880 μs) to 500 (2215 μs) are used. 45 mm hub divided by 300 is 0.15 mm. If you do the math for the  rotary motion, 180º divided by 300 points is 0.6º.

## Step 11: References

[1] Arduino: [ https://www.arduino.cc/](https://www.arduino.cc/)

[2] Servo library: [ https://www.arduino.cc/en/reference/servo](https://www.arduino.cc/en/reference/servo)

[3] Adafruit ServoShield: [ https://www.adafruit.com/product/1411](https://www.adafruit.com/product/1411)

[4] prfServo library: [ https://github.com/mrstefangrimm/prfServo](https://github.com/mrstefangrimm/prfServo)

[5] Arduino map function: [https://www.arduino.cc/reference/en/language/funct...](https://www.arduino.cc/reference/en/language/functions/math/map/)

[6] Example data set:
0 476
5 426
10 388
15 356
20 325
25 300
30 276
35 252
40 224
45 194

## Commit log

2018-12-26 Copied original LnR files from GRIS5A/Mechanics to the PA12_MjF branch.
    [LnR-ChassisHaube.skp, LnR-ChassisLinks.skp, LnR-ChassisRechts.skp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]
2018-12-26 Copied from GRis5A/Mechanics.
    [LnR-ChassisHaube.skp, LnR-ChassisLinks.skp, LnR-ChassisRechts.skp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]
2018-12-28 Initial Rev03 files.
    [LnR-ServoArmVerlaengerung.skp]
2018-12-28 Initial Rev03 files
    [LnR-ChassisHaube.skp, LnR-ChassisLinks.skp, LnR-Flansch-Kreuz.skp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]
2018-12-28 Added Accessories directory
    [LnR-Calibration-Basis.skp, LnR-Calibration-Messaufsatz.skp, LnR-Flansch.skp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]
2018-12-28 Updated photo and BOM
2018-12-29 Updated Sketchup models.
    [LnR-Calibration-Basis.skp, LnR-Calibration-Messaufsatz.skp, LnR-ChassisHaube.skp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]
2018-12-29 Replace LnR-Actuator.png sketch wich photo of parts.
2019-01-31 Improved stiffness.
    [LnR-ChassisHaube.skp, LnR-ChassisLinks.skp, LnR-ChassisRechts.skp]
2019-03-18 Corrected Bill Of Materials (BOM)
2020-02-22 Squashed commit of the following:
    commit 001a9d52d72614b3ab02954c1b3cff72f518c381
    Author: mrstefangrimm <motionsystems@grimm.com>
    Date: Sat Feb 22 11:20:12 2020 +0100
    Removed obsolete file
    commit 42b9a8f66eb65d939e4a79f8c899ed038c77d1c7
    Author: mrstefangrimm <motionsystems@grimm.com>
    Date: Sun Oct 13 18:20:14 2019 +0200
    Change BOM and Readme.
    commit 1ff4b539f8f7cb23dfcaca251c52c57d4d84a13d
    Author: mrstefangrimm <motionsystems@grimm.com>
    Date: Sun Aug 4 19:16:26 2019 +0200
    Replace sketchup files with files generated with SketchUp Shop.
    commit 0c26413a10630c090b86c8037341d23326b407b4
    Author: mrstefangrimm <motionsystems@grimm.com>
    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
    [LnR-ChassisHaube.skp, LnR-ChassisLinks.skp, LnR-ChassisRechts.skp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]
2020-04-12 Update Readme and add new SketchUp model.
    [LnR-Total.skp]
2020-04-25 Renamed accessory Sketchup models.
    [Cmn-FlanschHalter.skp, Gris5a-Flansch.skp]
2020-04-26 Update Readme and add SketchUp models for the JX9180MG servo.
    [LnR-Flansch-Kreuz-JX9180MG.skp, LnR-ReiterLinks-JX9180MG.skp, LnR-ReiterRechts-JX9180MG.skp]
2021-12-16 Squashed commit of the following:
    commit 31369a0b4b35b14a4672b88a1dc34174ef52ed13
    Date: Thu Dec 16 18:58:03 2021 +0100
    As published on instructables.
    commit 4995461b70f6de9d86ab7323d61e18e09648769c
    Date: Sun Dec 12 22:23:55 2021 +0100
    Add STL files and instructions.md
    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
    [LnR-AssembleBaseLeft.skp, LnR-AssembleServoArmExtension.skp, LnR-AssembleShafts.skp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]
2021-12-19 Improve build instructions.
    [LnR-ServoArmVerstaerkungsRing.stl, LnR-SliderLeftLid.stl, LnR-SliderRightLid.stl]
2022-11-26 Replace term "slider" with "carriage", "back side" with "rear plane", "carriage top" or "carriage cover" with "carriage lid".
    [LnR-CarriageLeft-JX9180MG.stl, LnR-CarriageLeft.stl, LnR-CarriageLeftLid.stl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]
2024-10-01 Add anguar web application (#1)
    * Add Software/lnr
    * Update Readme.
    [LnR-VirmsGroupCarriageAnthracite.obj, LnR-VirmsGroupCarriageBlue.obj, LnR-VirmsGroupCarriageGold.obj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]
2025-10-02 Add SketchUp model for servo arm long.

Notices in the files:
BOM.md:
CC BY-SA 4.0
